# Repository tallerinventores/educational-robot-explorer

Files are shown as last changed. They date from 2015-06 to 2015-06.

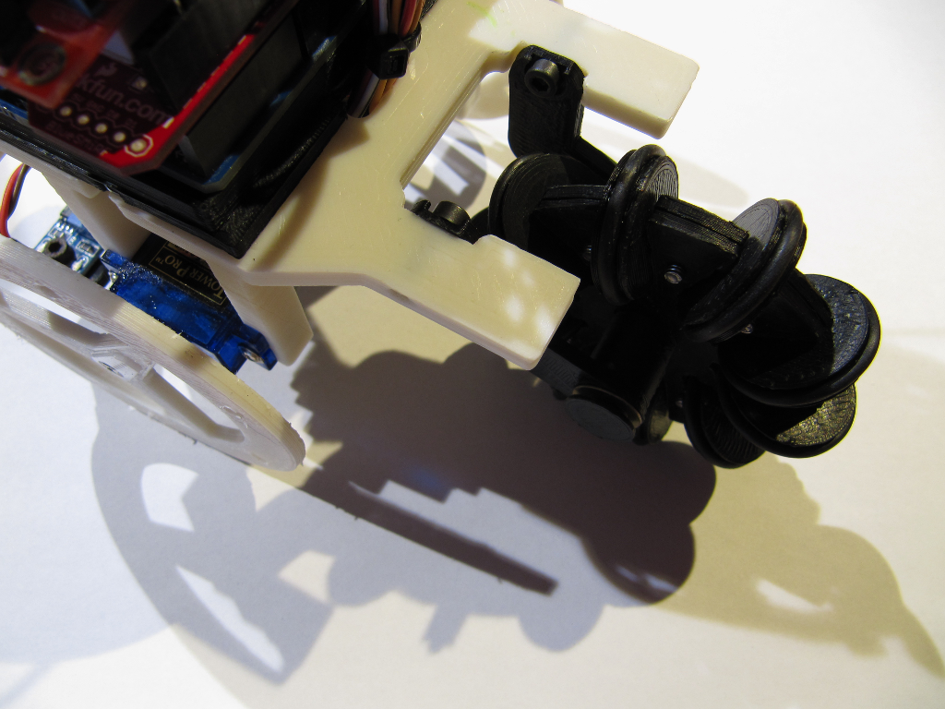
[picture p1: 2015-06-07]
img/photo-ere-2.png

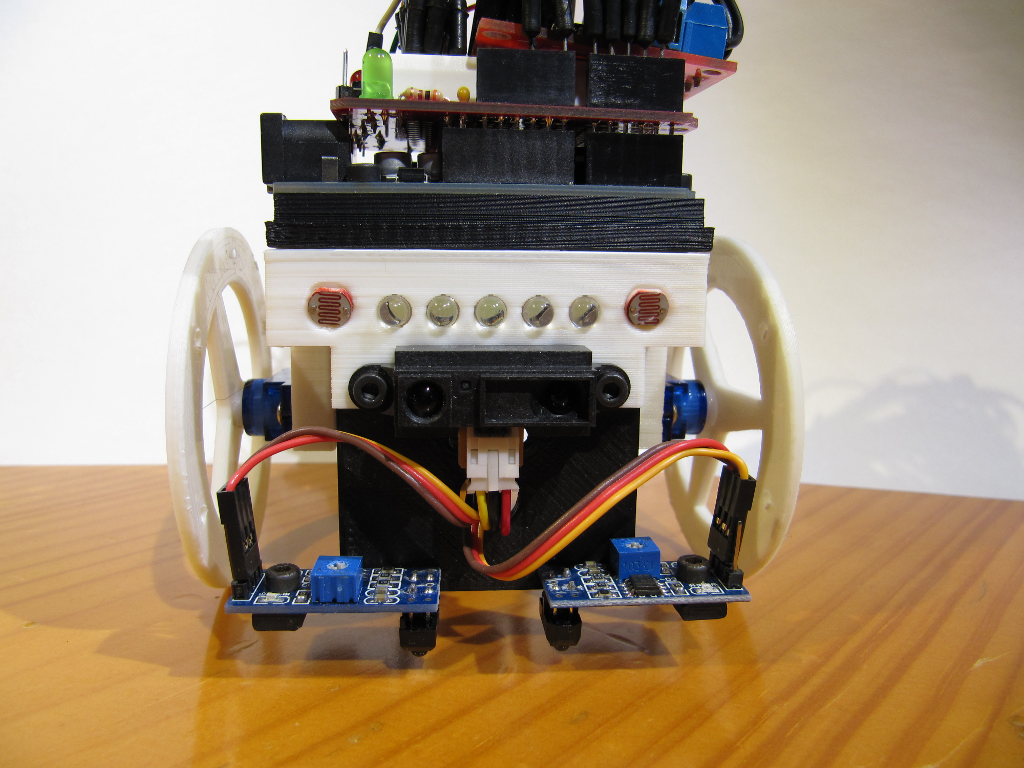
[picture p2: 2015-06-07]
img/photo-ere-4.png

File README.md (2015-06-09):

# Educational Robot Explorer #

> Generic rover robot for educational use

* * *

## Resumen ##

Explorador robótico para uso en entornos educativos. Ha sido desarrollado y
optimizado para impresión 3D y pensando en su bajo coste y facilidad de montaje
y uso. Es versátil al disponer de múltiples sensores y actuadores, por lo que
proporciona una plataforma de aprendizaje excelente.

## Instalación ##

En esta sección se cubre la instalación de software y hardware para el montaje
recomendado, mediante [Arduino](http://www.arduino.cc/).

### Requerimientos de software ###

Para poser usar Arduino (v1.6+) con el código fuente proporcionado, es necesario
[ArduinoFacil](https://github.com/tallerinventores/ArduinoFacil) una librería de
Arduino para principiantes. Para generar los archivos aptos para la impresora 3D
desde los archivos `.stl` será necesario adicionalmente un software para esta
función, como puede ser [Slic3r](http://slic3r.org/). El esquema eléctrico viene
detallado en archivo de [Fritzing](http://fritzing.org/home/)

Ver los requerimientos de mencionados programas previamente.

### Requerimientos de hardware ###

Será necesario para su montaje y uso una fuente de alimentación que proporcione
5W a 5V, un Arduino Uno o equivalente, dos servomotores tipo 9g modificados para
eliminar la lógica con sus correspondientes accesorios (tornillos y cuernos), y
los componentes listados en la sección «Conexión eléctrica». El rover está
optimizado para usar los servos **TowerPro SG90**. Adicionalmente harán falta
tornillos de métrica tres de diferentes largos.

## Uso ##

Instrucciones de montaje y puesta en marcha.

### Montaje del explorador robótico ###

1.  Imprimir una unidad de los archivos `clip.stl`, `fork_left.stl`,
    `fork_right.stl`, `shaft.stl`, `sensor.stl`, `arduino.stl`, `body.stl`.
    Imprimir dos unidades de `omni.stl`, `bigwheel.stl`. Imprimir diez unidades
    de `wheel.stl`. Puede ser necesario repasar las piezas impresas con el fin
    de eliminar rebabas.  
2.  Insertar un eje de 3mm (trozo de filamento) de nueve milimetros de largo en
    cada rueda pequeña (_wheel_). Colocar cada uno de ellos en las muescas de la
    rueda omnidireccional (_omni_) y cerrarlo con la otra mitad de la misma.
    Usar tornillos de M3x6 con tuerca o habiéndo hecho previamente rosca de M3
    en una de las mitades de la rueda omnidireccional. Puede resultar
    conveniente ajustar en cada rueda pequeña una junta tórica de 19mm.  
3.  Con las horquillas (_fork\_right_ y _fork\_left_) a los lados del montaje
    del punto anterior, sin que éstas tropiecen; insertar el pasador (_shaft_) a
    través del orificio central del conjunto. Asegurarlo en el extremo contrario
    con el clip (_clip_).  
4.  Encajar los led en los orificios del cuerpo del robot (_body_). Retenerlos
    si se considera necesario con algún tipo de adhesivo.  
5.  Colocar las dos ldr en los orificios destinados a ello del cuerpo, y fijarlo
    del mismo modo que con los led.  
6.  Atornillar con tornillos M3x10 el soporte de los sensores frontales
    (_sensor_) al cuerpo, pasando los tornillos previamente por el sensor de
    distancia. Pueden usarse tuercas o realizar rosca al soporte de los
    sensores.  
7.  Fijar los dos sensores reflectivos al soporte de sensores, quedando la
    óptica hacia el centro abajo. Usar para ello tornillos M3x6 con tuerca o con
    rosca sobre el soporte. Puede ser necesario doblar la cabecera de conexión
    para dejarla vertical u orientada hacia dentro.  
8.  Montar los dos servomotores con sus ejes hacia la parte forntal exterior y
    atornillarlos con los tornillos proporcionados con los servos.  
9.  Introducir los cuernos de los servos en las ruedas motrices (_bigwheel_) y
    fijarlo a los ejes de los servos con sus propios tornillos.  
10. Presentar el conjunto de la rueda omnidireccional en la parte trasera del
    cuerpo y atornillarlo usando tornillos de M3x10 si se ha realizado rosca o
    M3x16 y tuerca en caso contrario.  
11. Realizar la gestión de cables para conducir todos ellos a través de la
    abertura triangular del cuerpo.  
12. Encastrar tuercas en la base del Arduino (_arduino_), y atornillar la base
    al cuerpo con tornillos M3x10, con tuerca si no se ha realizado rosca en el
    cuerpo.  
13. Poner el Arduino sobre la base y atornillarlo con tornillos M3x10.  
14. Conectar los diferentes cables según el esquemático proporcionado.

### Conexión eléctrica ###

Seguir el montaje detallado en la carpeta `brd/`.

### Firmware ###

El Arduino deberá tener cargado el firmware incluido en la carpeta
`src/rover_base/`.

### Bugs ###

Se han observado los siguientes problemas:

-   Los servomotores pueden no girar con un factor de servicio menor al 50%.

## Enlaces externos ##

Este proyecto también está presente en:

-   [Thingiverse](http://www.thingiverse.com/thing:779589).

## Créditos ##

Proyecto realizado por Taller de Inventores 2015, representado por:

-   kwendenarmo <kwendenarmo@akornsys-rdi.net>

Alumnos de Centro de Formación Padre Piquer:

-   J, Pablo  
-   S, Eslendy  
-   S, Saul

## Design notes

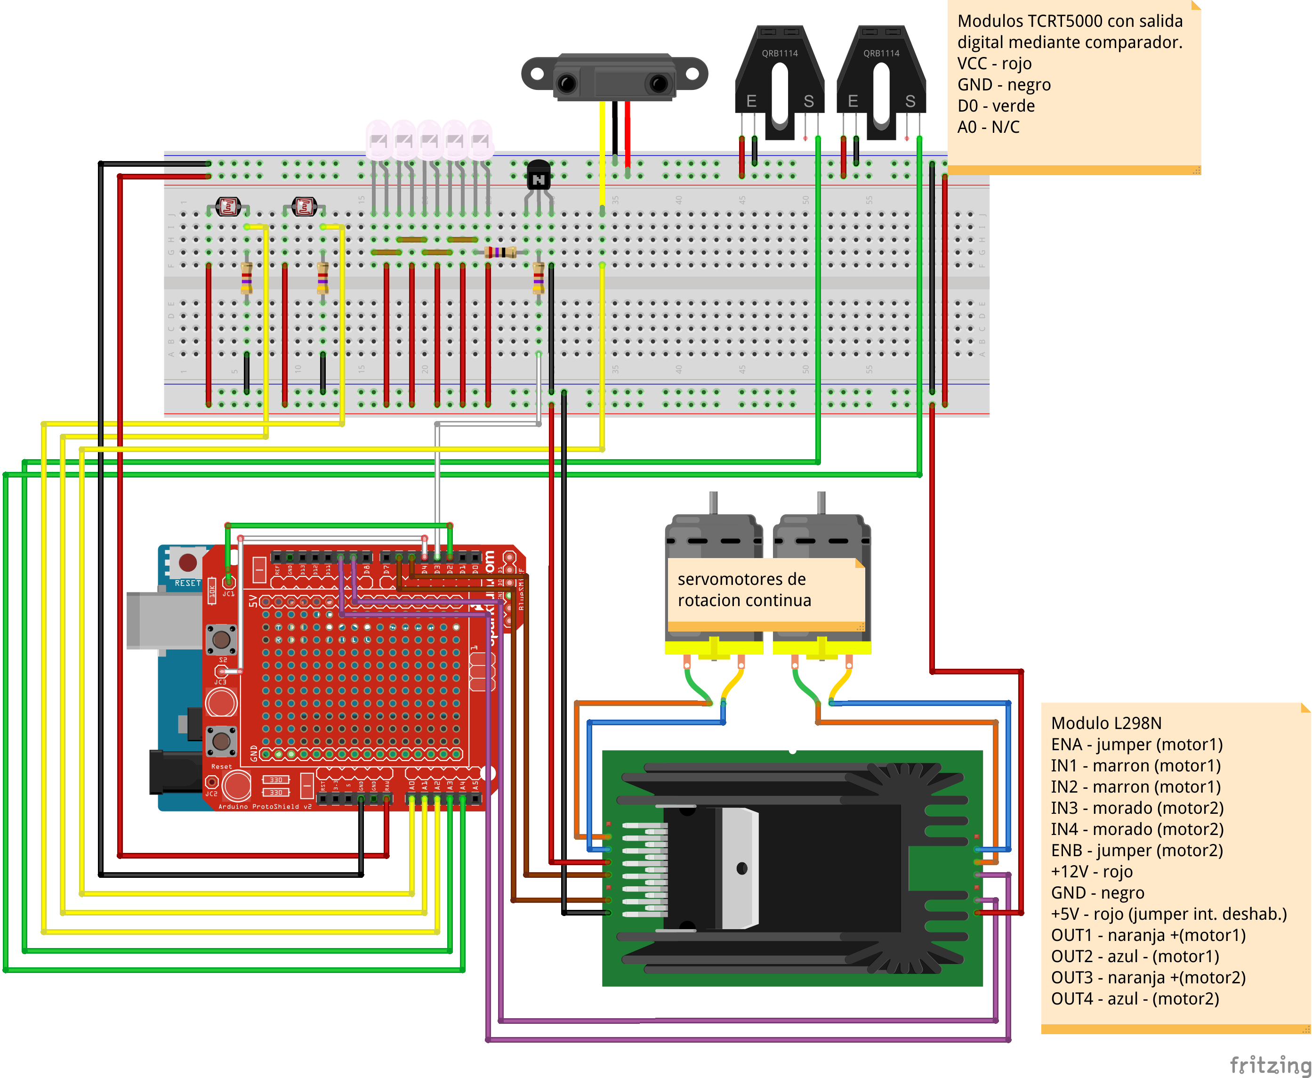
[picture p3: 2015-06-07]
img/schematic.png

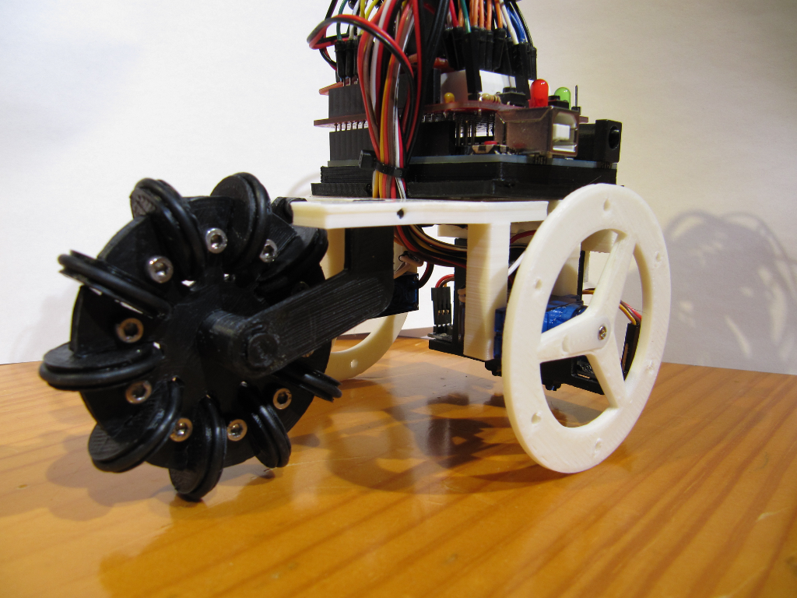
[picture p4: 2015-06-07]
img/photo-ere-5.png

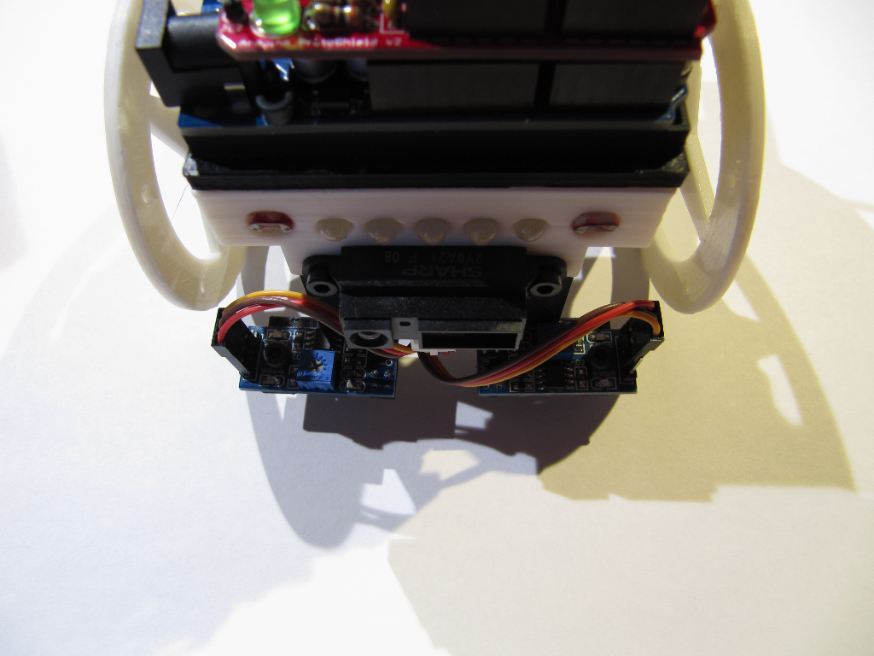
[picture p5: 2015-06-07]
img/photo-ere-1.png

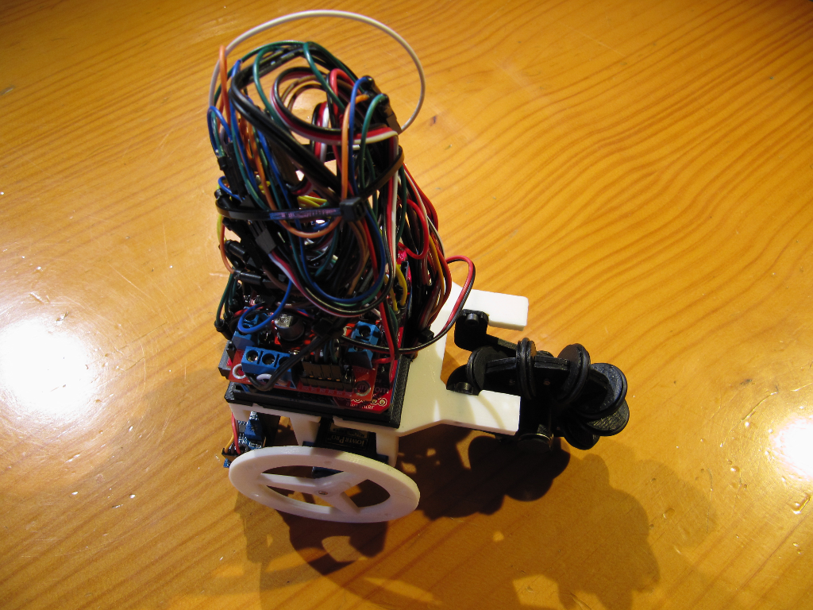
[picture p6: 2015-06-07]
img/photo-ere-3.png

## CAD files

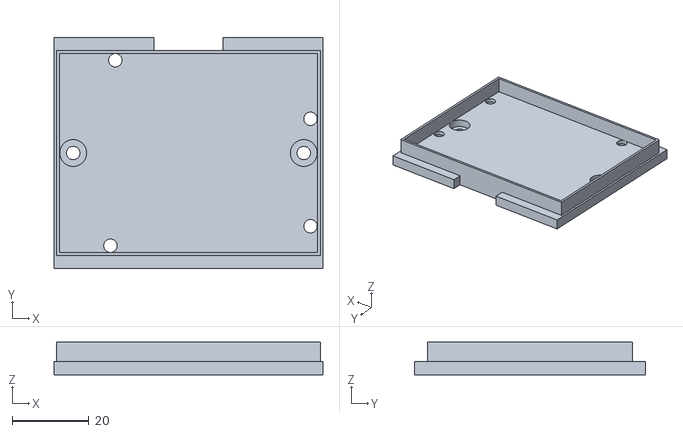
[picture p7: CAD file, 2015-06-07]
3d/arduino.stl
70.0 x 60.0 x 8.58

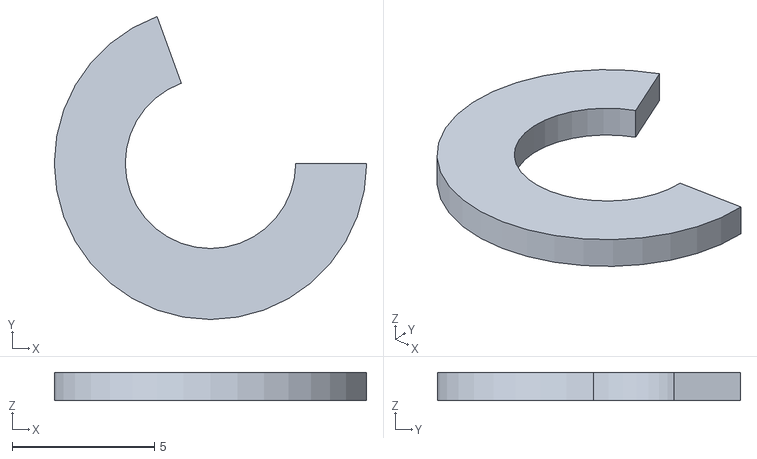
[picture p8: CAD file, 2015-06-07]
3d/clip.stl
11.0 x 10.7 x 1.00

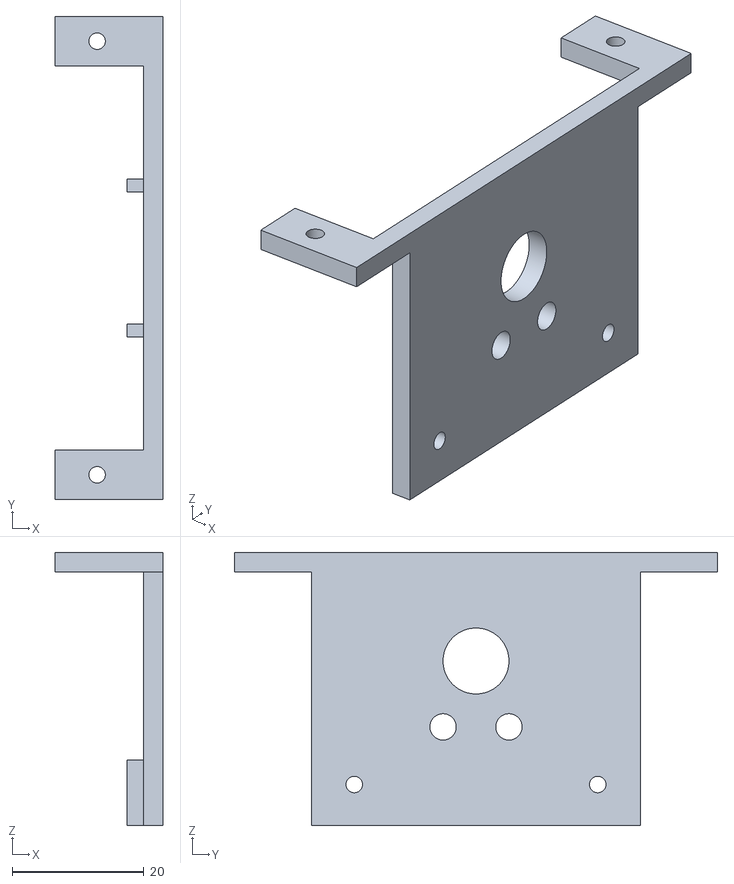
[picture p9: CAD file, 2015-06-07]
3d/sensor.stl
16.4 x 73.3 x 41.5

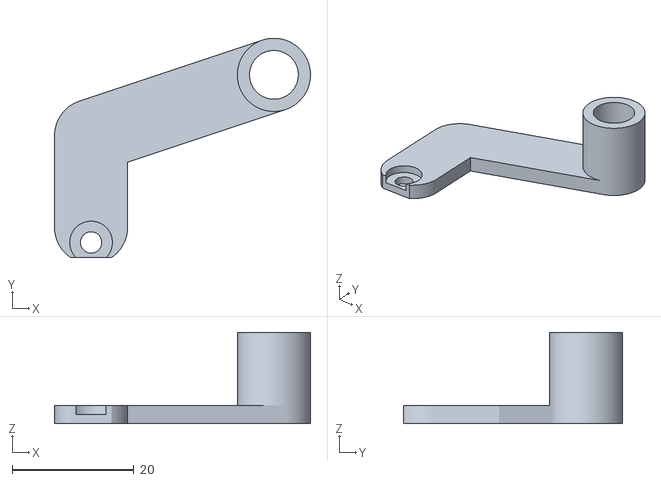
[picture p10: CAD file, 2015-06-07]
3d/fork_left.stl
42.0 x 36.0 x 15.0

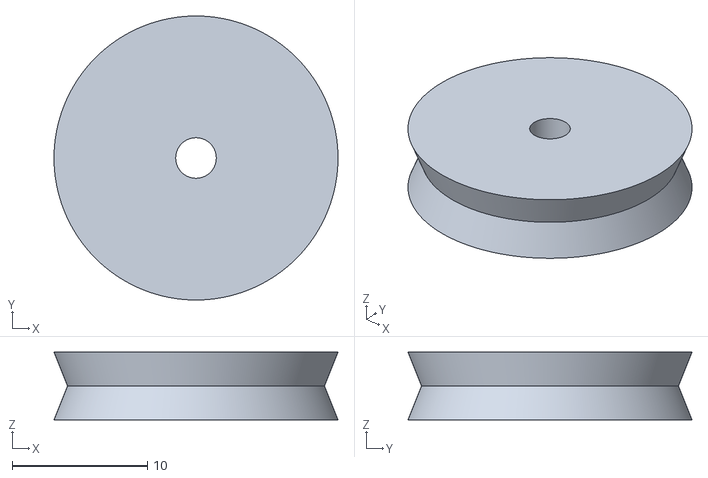
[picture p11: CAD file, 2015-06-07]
3d/wheel.stl
21.0 x 21.0 x 5.00

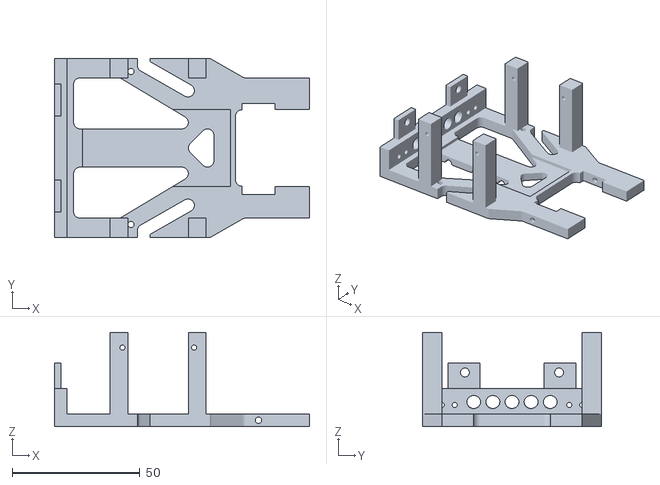
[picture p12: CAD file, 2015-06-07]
3d/body.stl
100.0 x 70.0 x 37.0

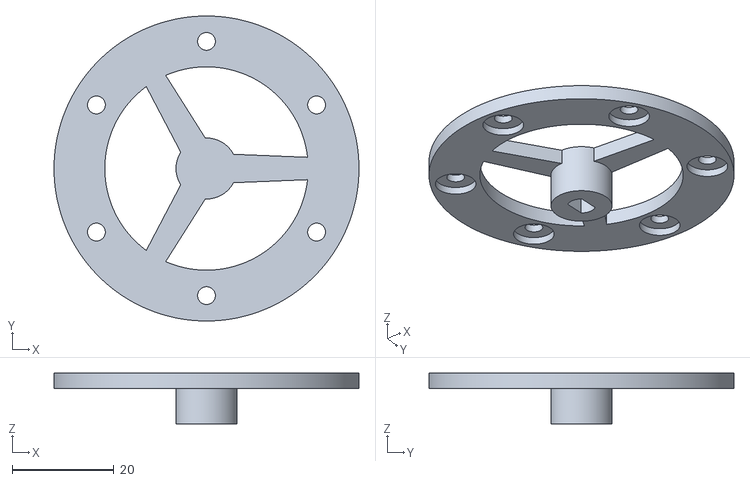
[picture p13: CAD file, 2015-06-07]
3d/combo.stl
60.0 x 60.0 x 10.0

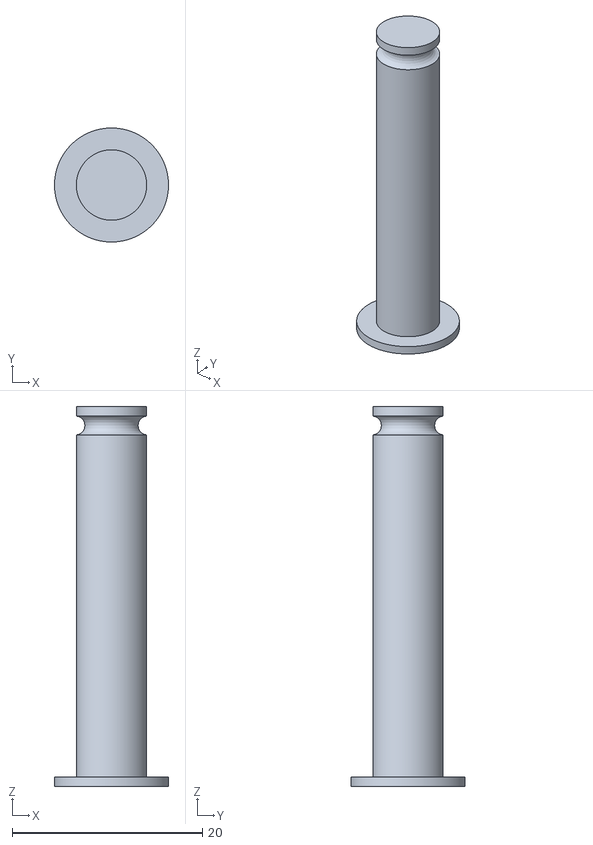
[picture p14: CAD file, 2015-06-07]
3d/shaft.stl
12.0 x 12.0 x 40.0

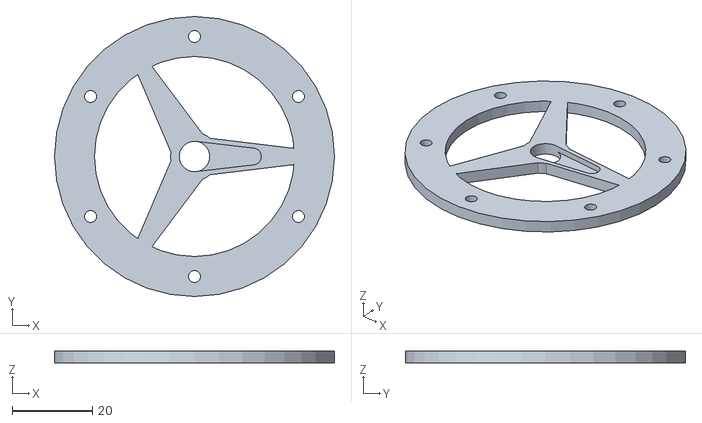
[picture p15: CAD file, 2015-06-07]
3d/bigwheel.stl
70.0 x 70.0 x 3.00

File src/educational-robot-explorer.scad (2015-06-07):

/* {{{ %%SECTION_HEADER%%
 * * * *
 * This header information is automatically generated by KodeUtils.
 *
 * File 'educational-robot-explorer.scad' edited by kwendenarmo,
 * last modified: 2015-06-06.
 * This file is part of 'educational-robot-explorer' package, please see
 * the readme files for more information about this file and this package.
 *
 * Copyright (C) 2015 by kwendenarmo <kwendenarmo@akornsys-rdi.net>
 * Released under the GNU GPLv3
 *
 *    This program is free software: you can redistribute it and/or modify
 *    it under the terms of the GNU General Public License as published by
 *    the Free Software Foundation, either version 3 of the License, or
 *    (at your option) any later version.
 *
 *    This program is distributed in the hope that it will be useful,
 *    but WITHOUT ANY WARRANTY; without even the implied warranty of
 *    MERCHANTABILITY or FITNESS FOR A PARTICULAR PURPOSE.  See the
 *    GNU General Public License for more details.
 *
 *    You should have received a copy of the GNU General Public License
 *    along with this program.  If not, see <http://www.gnu.org/licenses/>.
 *
 * * * *
 * %%EOS_HEADER%% }}}
 */

$fn=360;

assemble = true;
debug = false;
show_acc = true;

if (debug == true) {
    %translate([0,-20,68]) cube([1,110,1]); //floor
    %translate([0,25.5,68]) cube([1,19,2]); //line -- electrical tape
}

if ((debug == false) && (assemble == true)) {
    rotate([180,0,0]) union() {
        body();
        translate([30,35,0]) rotate([180,0,90]) porta_arduino();
        translate([2.5,10,15]) porta_sensor();
        if (show_acc == true) {
            translate([0,35,21.25]) rotate([-90,0,90]) sharp2y0a21();
            translate([6,20,10]) rotate([0,-90,0]) led_5mm();
            translate([6,27.5,10]) rotate([0,-90,0]) led_5mm();
            translate([6,35,10]) rotate([0,-90,0]) led_5mm();
            translate([6,42.5,10]) rotate([0,-90,0]) led_5mm();
            translate([6,50,10]) rotate([0,-90,0]) led_5mm();
            translate([2,60,8.5]) rotate([-65,0,90]) ldr();
            translate([2,10,8.5]) rotate([-65,0,90]) ldr();
            translate([0,26,53.4]) rotate([180,0,-90]) vishaytcrt5000();
            translate([-14.3,44,53.4]) rotate([180,0,90]) vishaytcrt5000();
            translate([35,-11.5,31]) rotate([90,180,0]) servo9g(0);
            translate([35,81.5,31]) rotate([-90,180,0]) servo9g(0);
            translate([10,20,5]) battery_pack();
        }
        translate([35,-12.5,31]) rotate([90,180,0]) bigwheel();
        translate([35,82.5,31]) rotate([-90,180,0]) bigwheel();
        translate([80,20,5]) rotate([90,0,0]) fork();
        mirror([0,1,0]) translate([80,-50,5]) rotate([90,0,0]) fork();
        translate([110,54.25,30]) rotate([90,0,0]) shaft();
        translate([110,35,30]) rotate([90,0,0]) omniwheel();
    }
}

if ((debug == false) && (assemble == false)) {
    //body();
    //porta_sensor();
    //porta_arduino();
    //fork();
    //mirror([0,0,1]) fork();
    //shaft();
    //clip();
    //omniwheel();
    //bigwheel();
    //wheel();
}

module body() {
    difference() {
        union() {
            cube([100,70,5]);
            translate([0,0,5]) cube([5,70,10]); //led + ldr
            translate([0,10,5]) cube([2.5,12.5,20]); //torre sharp dch
            translate([0,47.5,5]) cube([2.5,12.5,20]); //torre sharp izq
            translate([21.75,0,5]) cube([7,7.5,32]); //torre motor dch
            translate([52.5,0,5]) cube([7,7.5,32]); //torre motor dch
            translate([21.75,62.5,5]) cube([7,7.5,32]); //torre motor izq
            translate([52.5,62.5,5]) cube([7,7.5,32]); //torre motor izq
        }
        union() {
            //arduino
            translate([30,5,-1]) cylinder(r=1.25, h=7);
            translate([30,65,-1]) cylinder(r=1.25, h=7);
            //led
            for (i=[20:7.5:50]) {
                translate([-1,i,10]) rotate([0,95,0]) cylinder(r=2.75,h=7);
            }
            //ldr
            for (i=[10:50:60]) {
                translate([-2,i,10]) rotate([0,115,0]) cylinder(r=3.65,h=4);
                translate([-1,i+2.54,8.5]) rotate([0,90,0]) cylinder(r=1,h=7);
                translate([-1,i-2.54,8.5]) rotate([0,90,0]) cylinder(r=1,h=7);
            }
            //sharp
            translate([-1,53.475,21.25]) rotate([0,90,0]) cylinder(r=1.75,h=7);
            translate([-1,16.525,21.25]) rotate([0,90,0]) cylinder(r=1.75,h=7);
            //motores
            translate([26.65,-1,31]) rotate([-90,0,0]) cylinder(r=1, h=9);
            translate([54.75,-1,31]) rotate([-90,0,0]) cylinder(r=1, h=9);
            translate([26.65,62,31]) rotate([-90,0,0]) cylinder(r=1, h=9);
            translate([54.75,62,31]) rotate([-90,0,0]) cylinder(r=1, h=9);
            //porta baterias
            translate([11,20,3.5]) cube([58,30,3]);
            hull() {
                translate([17,25,0]) rotate([-90,0,0]) cylinder(r=2,h=20);
                translate([17,25,-1]) rotate([-90,0,0]) cylinder(r=2,h=20);
            }
            hull() {
                translate([32,25,0]) rotate([-90,0,0]) cylinder(r=2,h=20);
                translate([32,25,-1]) rotate([-90,0,0]) cylinder(r=2,h=20);
            }
            hull() {
                translate([47,25,0]) rotate([-90,0,0]) cylinder(r=2,h=20);
                translate([47,25,-1]) rotate([-90,0,0]) cylinder(r=2,h=20);
            }
            //fork
            translate([73.625,16.75,-1]) cube([12.75,4.25,7]);
            translate([73.625,48.25,-1]) cube([12.75,4.25,7]);
            translate([80,70,2.5]) rotate([90,0,0]) cylinder(r=1.25, h=70);
            //omniwheel
            translate([0,0,-1]) hull() {
                translate([73.5,22.5,0]) cylinder(r=2.5, h=7);
                translate([73.5,47.5,0]) cylinder(r=2.5, h=7);
                translate([105,22.5,0]) cylinder(r=2.5, h=7);
                translate([105,47.5,0]) cylinder(r=2.5, h=7);
            }
            //huecos
            translate([0,0,-1]) hull() {
                translate([10,10,0]) cylinder(r=2.5, h=7);
                translate([25,10,0]) cylinder(r=2.5, h=7);
                translate([10,25,0]) cylinder(r=2.5, h=7);
                translate([50,25,0]) cylinder(r=2.5, h=7);
            }
            translate([0,0,-1]) hull() {
                translate([10,60,0]) cylinder(r=2.5, h=7);
                translate([25,60,0]) cylinder(r=2.5, h=7);
                translate([10,45,0]) cylinder(r=2.5, h=7);
                translate([50,45,0]) cylinder(r=2.5, h=7);
            }
            translate([0,0,-1]) hull() {
                translate([35,67.4,0]) cylinder(r=2.5, h=7);
                translate([52.35,57.5,0]) cylinder(r=2.5, h=7);
            }
            translate([0,0,-1]) hull() {
                translate([35,70,0]) cylinder(r=2.5, h=7);
                translate([35,67.4,0]) cylinder(r=2.5, h=7);
            }
            translate([0,0,-1]) hull() {
                translate([35,2.6,0]) cylinder(r=2.5, h=7);
                translate([52.35,12.5,0]) cylinder(r=2.5, h=7);
            }
            translate([0,0,-1]) hull() {
                translate([35,0,0]) cylinder(r=2.5, h=7);
                translate([35,2.6,0]) cylinder(r=2.5, h=7);
            }
            translate([0,0,-1]) hull() {
                translate([57.5,-5,0]) cylinder(r=2.5, h=7);
                translate([75,5,0]) cylinder(r=2.5, h=7);
                translate([100,5,0]) cylinder(r=2.5, h=7);
                translate([100,-5,0]) cylinder(r=2.5, h=7);
            }
            translate([0,0,-1]) hull() {
                translate([57.5,75,0]) cylinder(r=2.5, h=7);
                translate([75,65,0]) cylinder(r=2.5, h=7);
                translate([100,65,0]) cylinder(r=2.5, h=7);
                translate([100,75,0]) cylinder(r=2.5, h=7);
            }
            translate([0,0,-1]) hull() {
                translate([55,35,0]) cylinder(r=2.5, h=7);
                translate([60,30,0]) cylinder(r=2.5, h=7);
                translate([60,40,0]) cylinder(r=2.5, h=7);
            }
        }
    }
}
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

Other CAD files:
3d/fork_right.stl

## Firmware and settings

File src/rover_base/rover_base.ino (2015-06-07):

/* Librerias */
#include <DistanceGP2Y0A21YK.h>
#include <ArduinoFacil.h>


/* Declaraciones */
declaraDistancia


/* Conexiones */
// 0    Reservado                  // 10   Motor 2 (derecho) bw
// 1    Reservado                  // 11   
// 2    Pulsador modo              // 12   
// 3    Luz frontal                // 13   Reservado
// 4    Led de estado              // A0   Sensor distancia
// 5    Motor 1 (derecho) bw       // A1   Sensor derecho luz
// 6    Motor 1 (derecho) fw       // A2   Sensor izquierdo luz
// 7                               // A3   Sensor derecho suelo
// 8                               // A4   Sensor izquierdo suelo
// 9    Motor 2 (derecho) fw       // A5   


/* Preparacion */
comienzoPreparacion
    iniciaPuerto
    estableceComoEntrada(2)     // pulsador
    estableceComoSalida(3)      // led frontales
    estableceComoSalida(4)      // led de estado
    estableceComoSalida(5)      // motor dch retroceso
    estableceComoSalida(6)      // motor dch avance
    estableceComoSalida(9)      // motor izq avance
    estableceComoSalida(10)     // motor izq retroceso
    iniciaDistancia(A0)         // sensor distancia
    estableceComoEntrada(A3)    // sensor suelo dch
    estableceComoEntrada(A4)    // sensor suelo izq
    generaSemilla(entradaAnalogica(A0))
finPreparacion


/* Receta */
comienzoReceta
    creaVariable(tiempo)
    creaVariable(prog)

    // Inicia el programa, esperando a que se pulse el botón o expiren 5 segundos
    enciende(4)
    esperaMientrasQue (cronometro esMenor que 5000 y entrada(2) esta ACTIVA) finEsperaMientrasQue
    si cronometro esMenor que 5000 entonces
        guardaValor(-1, prog)
    finSi
    apaga(4)
    espera(0.1)
    si prog noEsIgual a 0 entonces // El botón se ha pulsado
        
        // LEE PROGRAMA
        guardaValor(0, prog)
        espera(0.25)
        guardaValor(cronometro,tiempo)
        repetirMientrasQue(entrada(2) esta INACTIVA) entonces
            si (tiempo + 1000) esMenor que cronometro entonces
                guardaValor(cronometro,tiempo)
                enciende(4)
                incrementaValor(1,prog)
                espera(0.25)
                apaga(4)
            finSi
        finRepetirMientrasQue
        espera(0.5)
        repetir(i, prog)
            espera(0.25)
            enciende(4)
            espera(0.25)
            apaga(4)
        finRepetir
        espera(0.5)
        
        //PROGRAMA SIGUELUZ
        si prog esIgual a 1 entonces
            creaVariable(referencia_ldr_dch)
            creaVariable(valor_ldr_dch)
            creaVariable(diferencia_dch)
            creaVariable(referencia_ldr_izq)
            creaVariable(valor_ldr_izq)
            creaVariable(diferencia_izq)
            
            guardaValor(entradaAnalogica(A1), referencia_ldr_dch)
            guardaValor(entradaAnalogica(A2), referencia_ldr_izq)
            espera(0.1)
            porSiempre
                guardaValor(entradaAnalogica(A1), valor_ldr_dch)
                guardaValor(referencia_ldr_dch - valor_ldr_dch, diferencia_dch)
                guardaValor(entradaAnalogica(A2), valor_ldr_izq)
                guardaValor(referencia_ldr_izq - valor_ldr_izq, diferencia_izq)
                si diferencia_dch esMayor que (diferencia_izq + 100) entonces //gira a la derecha
                    enciende(4)
                    apaga(5)
                    enciendeConValor(6, 100) //rapido
                    apaga(10)
                    enciendeConValor(9, 40) //lento
                siSiNo diferencia_izq esMayor que (diferencia_dch + 100) entonces //gira a la izquierda
                    enciende(4)
                    apaga(5)
                    enciendeConValor(6, 50) //lento
                    apaga(10)
                    enciendeConValor(9, 85) //rapido
                siSiNo (diferencia_dch + diferencia_dch) esMayor que 200 entonces //sigue recto
                    enciende(4)
                    apaga(5)
                    enciendeConValor(6, 100) //rapido
                    apaga(10)
                    enciendeConValor(9, 85) //rapido
                siNo
                    apaga(4)
                    apaga(5)
                    apaga(6)
                    apaga(10)
                    apaga(9)
                finSi
                espera(0.05)
            finPorSiempre
        
        //PROGRAMA EVITA OBSTÁCULOS
        siSiNo prog esIgual a 2 entonces
            creaVariable(valor_distancia)
            
            porSiempre
                guardaValor(distancia, valor_distancia)
                si valor_distancia esMayor que 10 entonces //sigue recto
                    apaga(4)
                    apaga(5)
                    enciendeConValor(6, 75) //medio
                    apaga(10)
                    enciendeConValor(9, 64) //medio
                siNo //retrocede y gira
                    enciende(4)
                    apaga(5)
                    apaga(6)
                    apaga(9)
                    apaga(10)
                    espera(0.25)
                    enciendeConValor(5, 75) //retroceso
                    enciendeConValor(10, 67) //retroceso
                    espera(0.25)
                    si aleatorio(100) % 2 esIgual a 1 entonces
                        apaga(10)
                        enciendeConValor(9, 64) //medio
                    siNo
                        apaga(5)
                        enciendeConValor(6, 75) //medio
                    finSi
                    espera(0.5)
                finSi 
                espera(0.25)
                
            finPorSiempre
        
        //PROGRAMA SIGUELÍNEAS
        siSiNo prog esIgual a 3 entonces
            creaVariable(suelo_dch)
            creaVariable(suelo_izq)
            
            porSiempre
                guardaValor(entrada(A3), suelo_dch)
                guardaValor(entrada(A4), suelo_izq)
                si (suelo_dch esta ACTIVA y suelo_izq esta INACTIVA) entonces //gira a la izquierda
                    enciende(4)
                    apaga(5)
                    enciendeConValor(6, 50) //lento
                    apaga(10)
                    enciendeConValor(9, 85) //rapido
                siSiNo (suelo_izq esta ACTIVA y suelo_dch esta INACTIVA) entonces //gira a la derecha
                    enciende(4)
                    apaga(5)
                    enciendeConValor(6, 100) //rapido
                    apaga(10)
                    enciendeConValor(9, 40) //lento
                siSiNo (suelo_dch esta INACTIVA y suelo_izq esta INACTIVA) entonces //sigue recto
                    apaga(4)
                    apaga(5)
                    enciendeConValor(6, 100) //rapido
                    apaga(10)
                    enciendeConValor(9, 85) //rapido
                siNo
                    apaga(4)
                    apaga(5)
                    apaga(6)
                    apaga(9)
                    apaga(10)
                finSi
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
